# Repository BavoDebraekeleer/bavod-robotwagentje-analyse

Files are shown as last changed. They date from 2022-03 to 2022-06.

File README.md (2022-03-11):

# DocsifyJS Template 📒 🕸
> Starter template for a Markdown-based docs site







## Preview

<div align="center">
    <a href="https://michaelcurrin.github.io/docsify-js-template/">
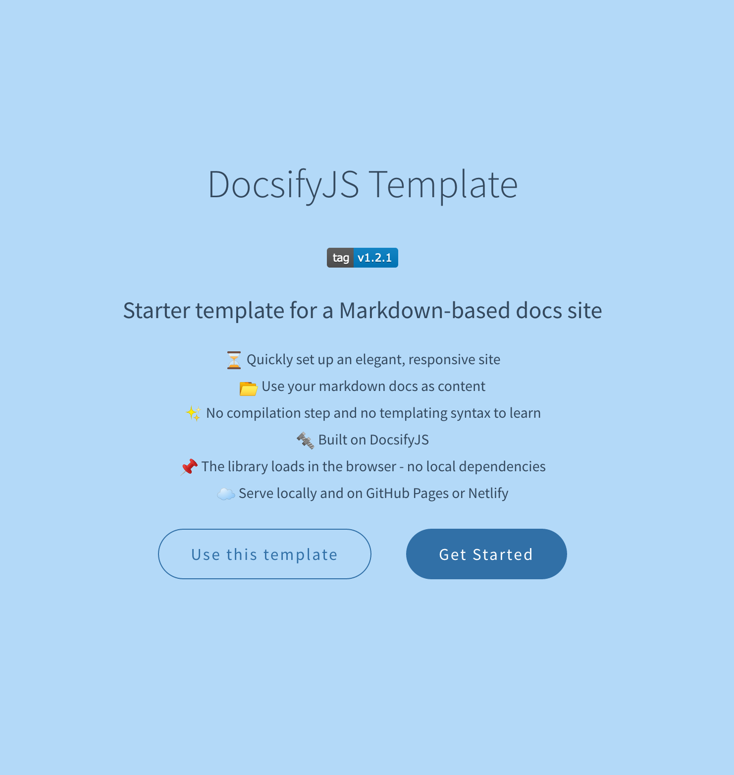
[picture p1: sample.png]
Sample screenshot
        
    </a>
</div>

<br>

<div align="center">



Instead of forking, rather make a new repo using this template button:



</div>

If you want to improve the original template, then fork it and make a PR.

## Features

- 🏭 Template for a SPA modern docs site.
- 📗 Use your awesome project's _existing_ markdown files.
- 🤩 Light on code – just add a single HTML file and optionally add cover page and navbar config.
- 🚀 Easy to host as a static site on GitHub Pages. No build step needed.

## Purpose
> How to use this project

- Create a **new repo** from the template and host it on GitHub Pages immediately. This is good for trying out Docsify or building a site project from scratch.
- Use this project as a **base** - follow instructions to download just the necessary files to your _existing_ repo's `docs` directory
- View the **live** demo site to see what you'll get.

For more info on Docsify, see my [DocsifyJS Tutorial][]. That covers intro to DocsifyJS, including installation, running and configuration. If you look at the repo, that has has more content and configuration than this relatively plain template site.

[DocsifyJS Tutorial]: https://michaelcurrin.github.io/docsify-js-tutorial/#/

## How to use Docsify in your projects

### Copy files

Use one of the approaches below to setup Docsify in your own project.

#### A. Use this template

Create a _new_ forked project based on this template  by clicking the button below. You'll get a fork in your own repo.



You could start adding code outside of the _docs_ directory, however this project is intended as a standalone docs site which can be configured for experimentation and used as reference.

#### B. Add Docsify to an existing project's docs directory

This will copy the contents of the docs directory from Github to the current folder - ideal if there is an existing project and you want to add to _Docsify_ it.

1. Ensure you have `curl` command installed. Or use `wget`.
2. Navigate to your project's `docs` folder.
    ```sh
    cd my-project/docs
    ```
3. Download necessary files in the template [docs](/docs) directory to your project using this two-line command. (The `-O` flag will save the files locally, keeping the original filenames.)
    ```sh
    REPO_DOCS='https://raw.githubusercontent.com/MichaelCurrin/docsify-js-template/master/docs/'
    curl $REPO_DOCS\{_coverpage.md,_sidebar.md,.nojekyll,index.html,README.md\} -O
    ```

### Customize

You can use your IDE to do find and replace across files.

Use the convenient [replace.sh](/replace.sh) script in this repo to replace the template's values with your own.

1. Find the script.
    - If you used the template button, you've already got it.
    - If adding content to your existing project's docs, copy script to your project **root** (not docs directory)
        ```sh
        curl 'https://raw.githubusercontent.com/MichaelCurrin/docsify-js-template/master/replace.sh' -O
        chmod +x ./replace.sh
        ```
2. Modify the `MY_` values then run this script to replace the template's value with your own.
3. Run the script from the **project root** against yours docs directory.
   ```sh
   ./replace.sh
   ```
4. The script can be deleted after you use it.

Now complete any remaining TODO items in the files.

### Use template readme

If you clicked _Use this template_, followed the customize steps above, then the last thing to do is replace the project's README.md file with the template one.

```sh
mv README.template.md README.md
```

Then customize README.md as your own project.

## Set up and run

### Remote use

Whatever approach you use to set up a `docs` directory, you can use your own project or a forked template and serve your site on platform like  GiHhub Pages or Netlify.

This template still works fine as a standalone online demo of _Docsify_ that you can tweak. In a real project, you'd add your code at the repo root, outside of `docs`. Or you could move your docs site to the repo root on the `gh-pages` branch for GH Pages.

### Serve locally

Follow this [gist](https://gist.github.com/MichaelCurrin/4c8060dcc9d8841f842eeebc7a1436d8) so you can view the docs site on a local webserver.

Go to my [DocsifyJS Tutorial - Serve locally](https://michaelcurrin.github.io/docsify-js-tutorial/#/?id=serve-a-docsify-site-locally) for more info on what DocsifyJS is and how to use it.

## Related projects

A template using Docsify Themeable. It is a Docsify site but easier to use, it is prettier (in my opinion), and supports a theme system that is more advanced than that in Docsify.

- 

A template for Vue-based docs site. Except it uses VuePress to render a static site (better for SEO) rather than as a Single-Page Application like Docsify.
 
- 

A template for a Vue-based app.

- 

## License

Released under [MIT](/LICENSE) by [@MichaelCurrin](https://github.com/MichaelCurrin).

- You can modify and reuse this project.
- Please link back to the original repo somewhere in your project if you use this in any way.
- Including an original license copy.
    - If you add content from [docs](/docs/) to your repo (or click _Use this template_) and then modify for your own needs so your copy is no longer a template, then you don't need to include a license.
    - If you do fork this repo then use it as your own _template_, then this project's license and copyright notice must be **included** with the software. [source](https://choosealicense.com/licenses/#mit). Copy `LICENSE` to `LICENSE-source` and then update your copy of `LICENSE` with your own details.

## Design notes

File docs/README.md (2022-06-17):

# Robotwagentje

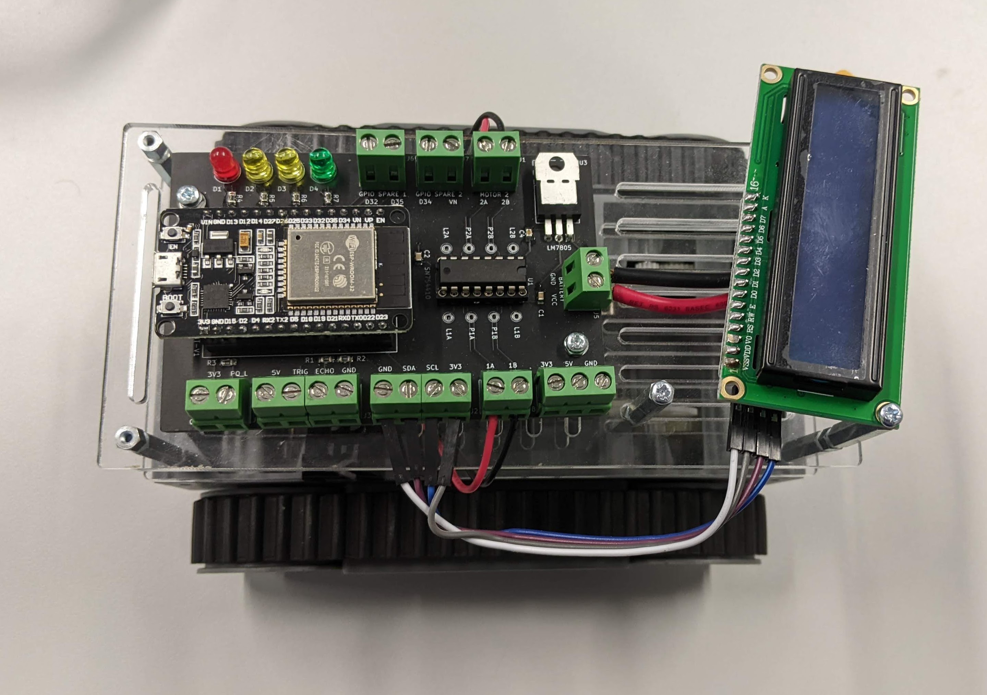
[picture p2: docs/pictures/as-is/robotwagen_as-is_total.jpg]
<br>

<br>

<br>
<br>
<br>
<br>
<br>
<br>

Bavo Debraekeleer<br>
Docent: Marc Smets en Maarten Luyts<br>

Smart Systems, major Internet of Things, Elektronica-ICT<br>
AP Hogeschool<br>
Academiejaar 2021-2022

<a href="https://bavodebraekeleer.github.io/bavod-robotwagentje-analyse/#/">Robotwagentje Analyse GitHub Pages</a><br>
<a href="https://ap-it-gh.github.io/ssys-cursus/#/deliverables/analyse">Smart Systems GitHub Pages</a><br>

---

# Probleemstelling

Ontwerp van een schakelingen om een robotwagentje aan te sturen.
Dit opgedeeld in twee deel schakelingen.
Een hoofd PCB met een ESP32, als ook een dochter PCB met een ATMega en sensoren om de sturing te kunnen realiseren.
De vereisten zijn omschreven in de To-Be Situatie.

---

## As-Is Situatie



Grote PCB met enkel through hole componenten en screw terminals.

Eigenschappen:
 - Gebruik ESP32-WROOM-32 Dev. Kit
 - Voltage Regulator LM7805 through hole
 - Motord river SN754410 through hole + 2x 2 motor pins: 1A, 1B, 2A, 2B
 - 4x LED's: 1x rood, 2x geel, 1x groen
 - LCD scherm module, I²C pins op PCB: GND, SDA, SCL, 3V3
 - Ultrasoon module aansluiting: 5V, TRIG, ECHO, GND
 - 3 voeding pins: 3V3, 5V, GND
 - 2 pin aansluiting: 3V3, PQ_L
 - 2x 2 GPIO spare pins

---

## To-Be Situatie of Systeemspecificaties

### Opdracht doelen

 - Sensoren toepassen in een praktische schakeling.
 - Voldoende materiaal genereren voor gebruik in het eerste jaar.
 - Besturing voorzien.

### Sturingsschakeling vereisten:

Dit is de hoofd PCB.

 - ESP32-WROVER-B microcontroller module zelf integreren in PCB.
 - SMD componenten gebruiken.
 - 2x UART connectoren
 - 3x I²C connectoren
 - Voltage regulator LDL1117 SMD
	- 5V
	- 3.3V
 - Polariteitsbeveiliging
 - 2x SMD Motor driver
	- 7.2V
	- 700mA (Start stroom = 6x nominale stroom)
	- Prijs < €1
	- EMK beveiligingsdiode in tegen polariteit. Misschien reeds aanwezig op IC. Best altijd extra diode bij plaatsen voor de zekerheid.
 - OLED-scherm met I²C-sturing op PCB
 - Mounting drill holes, voor bevestiging op wagentje
 - Batterij aansluiting (GND, VCC)

### Sensorenschakeling vereisten:

Samen op één dochter PCB of opgedeeld in meerdere PCB bordjes.

 - ATMega328p
 - Ultrasoon + IR afstandssensoren
 - 8 channel IR Line tracker

### Besturing

 - Modus selectie
 - Manuele bediengingsmodus
 - Automatisch rijden (afstandsmetingen)
 - Volgens vast patroon rijden (lijn volgen)

Er moeten ook een aantal verkeer signalisaties ontwikkeld worden zoals verkeerslichten, slagbomen, enz.<br>
Deze moeten dienen om de software van het wagentje te kunnen testen.

---

## Mindmap

### Interactieve Mindmap
<iframe width="1000" height="1000" src="https://miro.com/app/embed/uXjVOER2lsE=/?pres=1&frameId=3458764521281290834" frameBorder="0" scrolling="no" allowFullScreen></iframe>

### Mindmap afbeelding
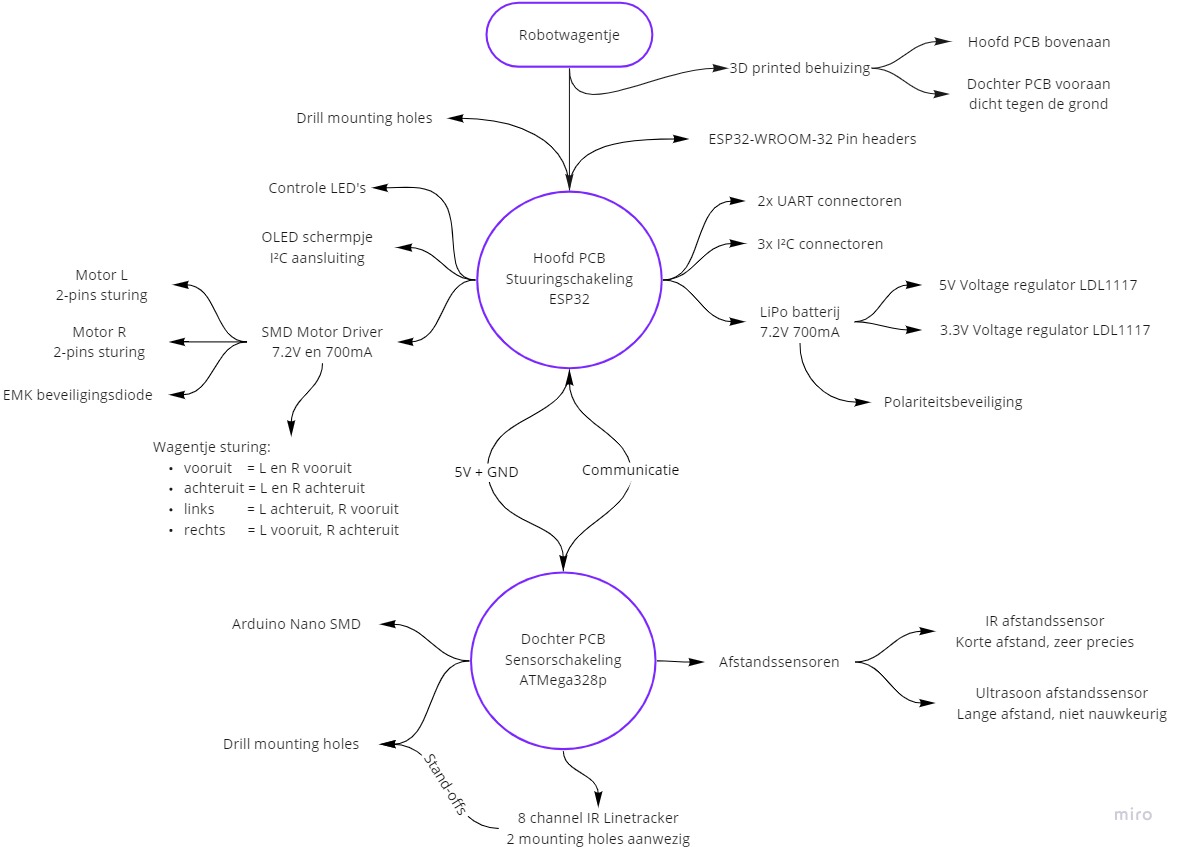
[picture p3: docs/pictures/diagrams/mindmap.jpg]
Mindmap afbeelding
<br>
<a href="./pictures/diagrams/mindmap.jpg">Minddmpa afbeelding openen.</a><br>

---

# Hardware Analyse

## Blokschema

### Interactief Blokschema
<iframe width="1000" height="1000" src="https://miro.com/app/embed/uXjVOEQMNko=/?pres=1&frameId=3458764523376607643" frameBorder="0" scrolling="no" allowFullScreen></iframe>

### Blokschema afbeelding
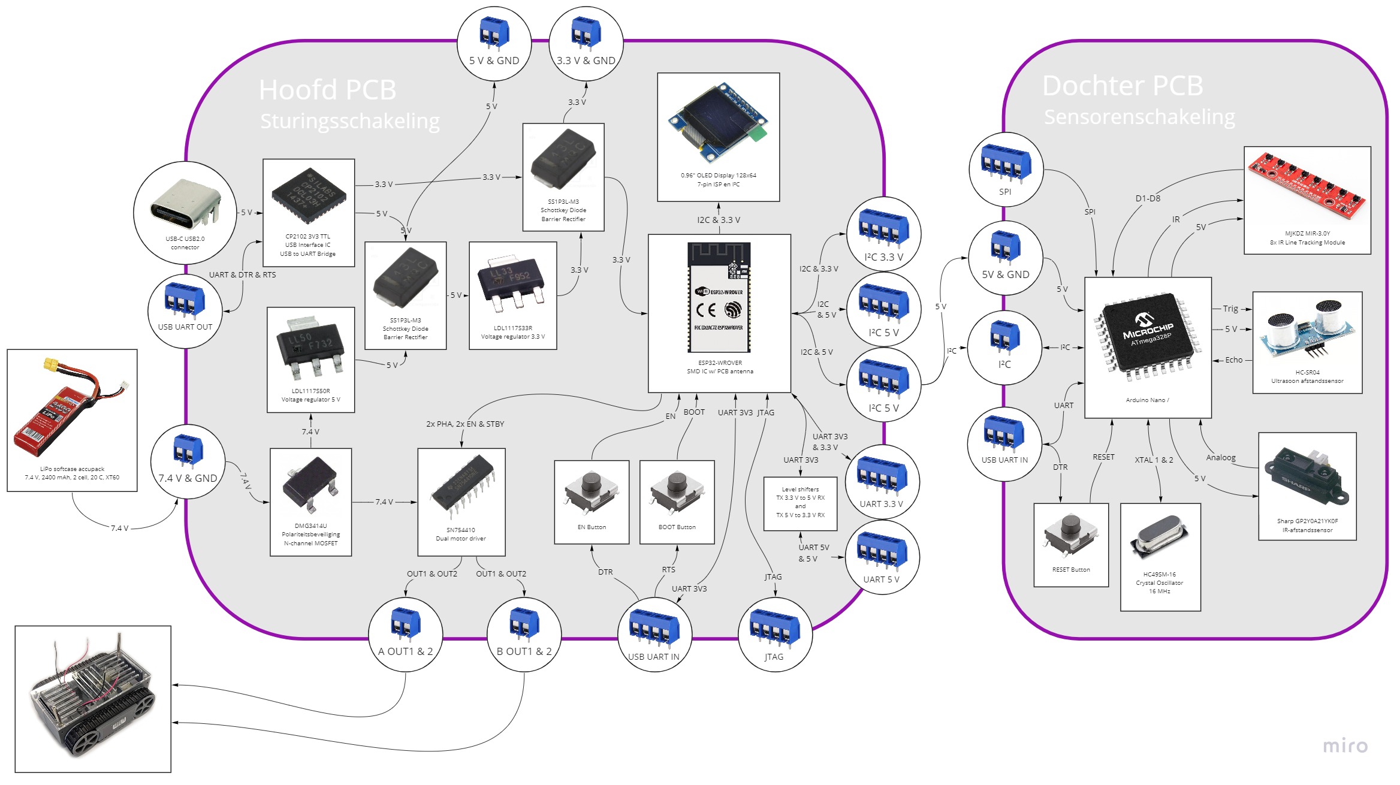
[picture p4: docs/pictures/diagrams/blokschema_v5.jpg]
Blokschema afbeelding
<br>
<a href="./pictures/diagrams/blokschema_v5.jpg">Blokschema afbeelding openen.</a><br>

---

## Specificaties

Reference websites:
 - <a href="https://be.farnell.com/">Farnell</a><br>
 - <a href="https://www.mouser.be/">Mouser</a><br>
 - <a href="https://www.digikey.be/">Digi-Key</a><br>
 - <a href="https://www.tinytronics.nl/shop/nl">TinyTronics</a><br>
 - <a href="https://octopart.com/">Octopart</a><br>
 - <a href="https://componentsearchengine.com/">Component Search Engine</a><br>

### Hoofd PCB: Sturingsschakeling

#### Microcontroller

<table style="width: 100%">
<colgroup>
    <col span="1" style="width: 15%;">
    <col span="2" style="width: 30%;">
    <col span="3" style="width: 40%;">
	<col span="4" style="width: 25%;">
</colgroup>
<tr>
    <th>Naam</th>
    <th>Eigenschappen</th>
    <th>Argumentatie</th>
    <th>Data</th>
</tr>
<tr>
    <td>ESP32-WROVER</td>
    <td>
        <ul>
            	<li><b>ESP32 REV1 microcontroller</b></li>
		<li>Core: ESP32-D0WDQ6</li>
		<li>SPI flash: 4 MB, 32 Mbits, 3.3 V</li>
		<li>PSRAM: 64Mbits</li>
		<li>Crystal: 40 MHz</li>
            	<li>V<sub>cc</sub> = 3.0 - 3.6 V</li>
            	<li>I<sub>operating</sub> = 80 mA</li>
		<li>I<sub>min delivered by power supply</sub> = 500 mA</li>
		<li>Module interfaces: SD card, UART, SPI, SDIO, I2C, LED PWM, Motor PWM, I2S, IR, pulse counter, GPIO, capacitive touch sensor, ADC, DAC, TWAI.</li>
		<li>On-chip sensor: Hall sensor</li>
		<li>Operating temperature: -40°C ~ +85°C</li>
		<li><i>Eenheidsprijs: €5,50</i></li>
		<li><i>Lead time: onbekend (op voorraad)</i></li>
        </ul>
    </td>
	<td>
		ESP32 module die beschikbaar is in het labo.
	</td>
    <td>
		<a href="./datasheets/esp32-wrover_datasheet_en-1223875.pdf">Datasheet Module</a><br>
		<a href="./datasheets/esp32_datasheet_en.pdf">Datasheet ESP32</a><br>
		<a href="./datasheets/esp32_hardware_design_guidelines_en.pdf">Hardware Design Guidelines</a><br>
		<a href="https://www.tinytronics.nl/shop/nl/communicatie-en-signalen/draadloos/wi-fi/modules/esp32-wrover-wifi-module-pcb-antenne-aansluiting">Winkel TinyTronics</a><br>
	</td>
</tr>
<tr>
    <td>ESP32-WROOM-32</td>
    <td>
        <ul>
            	<li><b>ESP32 microcontroller</b></li>
		<li>Core: ESP32-D0WD</li>
		<li>SPI flash: 4 MB, 32 Mbits, 3.3 V</li>
		<li>Crystal: 40 MHz</li>
            	<li>V<sub>cc</sub> = 3.0 - 3.6 V</li>
            	<li>I<sub>operating</sub> = 80 mA</li>
		<li>I<sub>min delivered by power supply</sub> = 500 mA</li>
		<li>Module interfaces: SD card, UART, SPI, SDIO, I2C, LED PWM, Motor PWM, I2S, IR, pulse counter, GPIO, capacitive touch sensor, ADC, DAC, TWAI.</li>
		<li>On-chip sensor: Hall sensor</li>
		<li>Operating temperature: -40°C ~ +85°C</li>
		<li><i>Eenheidsprijs: €4,68</i></li>
		<li><i>Lead time: 10 weken (op voorraad)</i></li>
        </ul>
    </td>
	<td>
		Alternatieve versie van de ESP32 module.
	</td>
    <td>
		<a href="./datasheets/esp32_wroom_32d_esp32_wroom_32u_datasheet_en-1365844.pdf">Datasheet Module</a><br>
		<a href="./datasheets/esp32_datasheet_en.pdf">Datasheet ESP32</a><br>
		<a href="./datasheets/esp32_hardware_design_guidelines_en.pdf">Hardware Design Guidelines</a><br>
		<a href="https://www.digikey.be/nl/products/detail/espressif-systems/ESP32-WROOM-32/8544298">Winkel Digi-Key</a><br>
		<a href="https://www.elektor.nl/wemos-lolin-esp32-oled-display-module-for-arduino"Alternatieve kit met OLED</a><br>
	</td>
</tr>
</table>

#### Sturing

<table style="width: 100%">
<colgroup>
    <col span="1" style="width: 15%;">
    <col span="2" style="width: 30%;">
    <col span="3" style="width: 40%;">
	<col span="4" style="width: 25%;">
</colgroup>
<tr>
    <th>Naam</th>
    <th>Eigenschappen</th>
    <th>Argumentatie</th>
    <th>Data</th>
</tr>
<tr>
    <td>SN754410NE</td>
    <td>
        <ul>
            	<li><b>Quadruple Half-H Driver</b></li>
		<li>Through-hole IC met 2 drivers</li>
		<li>Package: DIP</li>
            	<li>V<sub>cc</sub> = -0.5 - +36 V</li>
		<li>V<sub>O</sub> = -3 - +3 V</li>
            	<li>I<sub>O</sub> = ±1 A</li>
		<li>Power dissipation P<sub>D</sub> = 2.078 W</li>
		<li>Minimized Power Dissipation</li>
		<li><i>Eenheidsprijs: 2,93 - 2,48€</i></li>
		<li><i>Lead time: 26 weken (op voorraad)</i></li>
        </ul>
    </td>
    <td>
	    	Motor driver through-hole als vervanging door laattijdige beschikbaarheid van de TC78H621FN.
	    	Deze is duurder, maar was reeds beschikbaar in het labo.
	    	Heeft ook een veel betere power dissipatie.
	    	
	</td>
    <td>
		<a href="./datasheets/sn754410.pdf">Datasheet</a><br>
	    	<a href="https://www.ti.com/product/SN754410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">Website fabrikant</a><br>
		<a href="https://be.farnell.com/texas-instruments/sn754410ne/ic-peripheral-driver-half-h-1a/dp/3118977?ost=SN754410">Winkel Farnell</a><br>
	</td>
</tr>
<tr>
    <td>TC78H621FNG</td>
    <td>
        <ul>
            	<li><b>Stepping motor drivers</b></li>
		<li>Full, Half step resolution / Phase inputs</li>
		<li>2-phase bipolar stepper + full bridge driver</li>
		<li>SMD IC met 2 drivers</li>
		<li>Package: P-TSSOP16-0505-0.65-001</li>
            	<li>V<sub>cc</sub> = 2.8 - 14 V</li>
		<li>V<sub>OUT</sub> = 18 V</li>
            	<li>I<sub>OUT</sub> = 1.1 A</li>
		<li>Power dissipation P<sub>D</sub> = 0.78 W</li>
		<li><i>Eenheidsprijs: 1,66 - 0,82€</i></li>
		<li><i>Lead time: 26 weken (op voorraad)</i></li>
        </ul>
    </td>
    <td>
	    	Motor driver aangegeven door docent als te gebruiken IC en op voorraad in het labo.
	    	
	</td>
    <td>
		<a href="./datasheets/TC78H621FNG_TOSC-S-A0003869562-1.pdf">Datasheet</a><br>
	    	<a href="https://toshiba.semicon-storage.com/ap-en/semiconductor/product/motor-driver-ics/stepping-motor-driver-ics/detail.TC78H621FNG.html">Website fabrikant</a><br>
		<a href="https://www.digikey.com/en/products/detail/toshiba-semiconductor-and-storage/TC78H621FNG-EL/9351603">Winkel Digi-Key</a><br>
	</td>
</tr>
<tr>
    <td>LA6583MC-AH</td>
    <td>
        <ul>
            	<li><b>Motor driver</b></li>
		<li>Single Phase Driver With Hall Sensor Method (no Speed Control)</li>
		<li>SMD IC</li>
		<li>Output Configuration: Half Bridge, 2 outputs</li>
            	<li>V<sub>cc</sub> = 2.8 - 14 V</li>
		<li>V<sub>cc max</sub> = 15 V</li>
		<li>I<sub>cc drive</sub> = 4 - 6 - 9 mA</li>
            	<li>I<sub>OUT max</sub> = 800 mA</li>
		<li><i>Eenheidsprijs: 0,526€</i></li>
		<li><i>Lead time: onbekend (op voorraad)</i></li>
        </ul>
    </td>
    <td>
	    	Alternatieve Motor Driver als eerste voorgesteld door docent.
		Deze Motor Driver heeft twee outputs en wordt gebruikt om één motor aan te sturen in twee richtingen.
		Voor twee motors zijn er dus twee nodig in de schakeling.
		Een enkele IC om de twee motors aan te sturen komt veel duurder uit of zijn niet op voorraad.
		<a href="https://www.mouser.be/ProductDetail/Toshiba/TB6612FNGC8EL?qs=rsevcuukUAy2UalRuv4E%2FQ%3D%3D">Alternatief: TB6612FNG</a><br>
	</td>
    <td>
		<a href="./datasheets/LA6583MC-AH.pdf">Datasheet</a><br>
		<a href="https://be.farnell.com/on-semiconductor/la6583mc-ah/mtr-drvr-sngl-phase-fan-motor/dp/2728202?st=LA6583MC-AH">Winkel</a><br>
	</td>
</tr>
<tr>
    <td>Merkloos OLED 0.96" SPI</td>
    <td>
        <ul>
		<li><b>0.96" OLED Display 128x64</b></li>
		<li>V<sub>cc</sub> = 3.3 - 5 V</li>
		<li>I<sub>cc</sub> = 9 - 15 mA</li>
		<li>Controller: SSD1315</li>
		<li>Comm protocol: SPI of I²C</li>
		<li>Connector: 7 PIN's</li>
		<li>Afmetingen: 27.8 x 27.3 x 4.3 mm</li>
		<li>Drill holes: 2 mm diameter, ~1 mm van de rand</li>
		<li><i>Eenheidsprijs: €4,60 - €7,00</i></li>
		<li><i>Lead time: onbekend (op voorraad)</i></li>
        </ul>
    </td>
    <td>
		Er wordt hier gekozen voor een module omdat losse OLED displays moeilijk vindbaar zijn en/of duurder uitkomen, en meer werk zijn.
		Deze merkloze verzie is op voorraad in het labo en kan werken op I²C mits kleine aanpassingen aan de PCB.
		I²C aansluitingen: D0 = SCL, D1 = SDA, DC & CS = GND, RST = Solderen
		Goedkoper alternatief: Seeed Studio Grove 104020208
		<a href="https://www.distrelec.biz/en/ssd1315-grove-96-128-64-monochrome-oled-display-seeed-studio-104020208/p/30164993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">Winkel Distrelec</a><br>
		<a href="https://wiki.seeedstudio.com/Grove-OLED-Display-0.96-SSD1315/">Fabrikant product info</a><br>
		Enkele alternatieven van TinyTronics met I²C PIN connectors in meerdere formaten:
		<a href="https://www.tinytronics.nl/shop/nl/displays/oled/0.96-inch-oled-display-128*64-pixels-wit-i2c">0.96" 128x64 SSD1306 voor €7,00</a><br>
		<a href="https://www.tinytronics.nl/shop/nl/displays/oled/1.3-inch-oled-display-128*64-pixels-wit-i2c">1.3" 128x64 SSH1106 voor €8,00</a><br>
		<a href="https://www.tinytronics.nl/shop/nl/displays/oled/1.5-inch-oled-display-128*128-pixels-wit-i2c">1.5" 128x128 SSD1327 voor €10,00</a><br>
		 <a href="https://www.tinytronics.nl/shop/nl/kabels-en-connectoren/kabels-en-adapters/jst-compatible/wemos-i2c-kabel-sh1.0-4p-10cm">JST 4P kabel I²C</a><br>
		<a href="https://www.tinytronics.nl/shop/nl/kabels-en-connectoren/connectoren/jst-compatible/jst-xh-krimpstekker-en-behuizing-set">JST-HX stekkers set</a><br>
	</td>
    	<td>
		<a href="./datasheets/OEL_Display_Module_SJY-2864KSWPG01.pdf">OLED Module Datasheet</a><br>
		<a href="https://www.tinytronics.nl/shop/nl/displays/oled/0.96-inch-oled-display-128*64-pixels-blauw">Winkel TinyTronics</a><br>
		<a href="https://github.com/olikraus/u8g2">Bibliotheek: U8g2</a><br>
	</td>
</tr>
</table>

#### Voeding

<table style="width: 100%">
<colgroup>
    <col span="1" style="width: 15%;">
    <col span="2" style="width: 30%;">
    <col span="3" style="width: 40%;">
	<col span="4" style="width: 25%;">
</colgroup>
<tr>
    <th>Naam</th>
    <th>Eigenschappen</th>
    <th>Argumentatie</th>
    <th>Data</th>
</tr>
<tr>
    <td>Conrad Energy LiPo accupack</td>
    <td>
        <ul>
            	<li><b>LiPo softcase accupack</b></li>
            	<li>V<sub>nomonaal</sub> = 7.4 V</li>
            	<li>I<sub>nominaal</sub> =  1200 mAh</li>
		<li>Aantal cellen: 2</li>
		<li>Belastbaarheid: 20 C</li>
		<li>Aansluiting: XT60, XH-balancer</li>
		<li>Afmetingen: 112 x 35 x 19 mm</li>
		<li><i>Eenheidsprijs: €16,49</i></li>
		<li><i>Lead time: onbekend (op voorraad)</i></li>
        </ul>
    </td>
    <td>
		Zelfde batterij als in de As-Is situatie blijft behouden.
	</td>
    <td>
		<a href="./datasheets/accu.pdf">Datasheet</a>
		<a href="https://www.conrad.be/nl/p/conrad-energy-lipo-accupack-7-4-v-2400-mah-aantal-cellen-2-20-c-softcase-xt60-1344133.html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">Winkel Conrad</a><br>
	</td>
</tr>
<tr>
    <td>LDL1117S50R</td>
    <td>
        <ul>
            	<li><b>Voltage Regulator 5 V</b></li>
		<li>Package: SOT223 SMD</li>
		<li>V<sub>output</sub> = 5 V</li>
            	<li>V<sub>input</sub> = 2.5 - 18 V</li>
            	<li>I<sub>output</sub> = 1.2 A</li>
		<li><i>Eenheidsprijs: €0,56</i></li>
		<li><i>Lead time: 52 weken (lage voorraad)</i></li>
        </ul>
    </td>
    <td>
		Eenvoudige en goedkope LDO regulator.
		Alternatieven die 3.3 en 5 V in één package doen hebben een lage I<sub>output</sub>.
		Alternatief voorbeeld:
		<a href="https://www.mouser.be/ProductDetail/Microchip-Technology-Micrel/MIC5211-LXYM6-TR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">MIC5211-LXYM6-TR</a>
    </td>
    <td>
		<a href="./datasheets/LDL1117_algemeen.pdf">Datasheet algemeen</a><br>
		<a href="./datasheets/LDL1117_SOT223_specific.pdf">Datasheet SOT223</a><br>
		<a href="https://www.mouser.be/ProductDetail/STMicroelectronics/LDL1117S50R?qs=AQlKX63v8RsuN9BQFiVf%2Fg%3D%3D">Winkel Mouser</a><br>
		<a href="https://www.avnet.com/shop/us/products/stmicroelectronics/ldl1117s50r-3074457345642528941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">Winkel AVNET (op voorraad)</a>
	</td>
</tr>
</table>
<table style="width: 100%">
<colgroup>
    <col span="1" style="width: 15%;">
    <col span="2" style="width: 30%;">
    <col span="3" style="width: 40%;">
	<col span="4" style="width: 25%;">
</colgroup>
<tr>
    <td>LDL1117S33R</td>
    <td>
        <ul>
            	<li><b>Voltage Regulator</b></li>
		<li>Package: SOT-223 SMD</li>
		<li>V<sub>output</sub> = 5 V</li>
            	<li>V<sub>input</sub> = 2.5 - 18 V</li>
            	<li>I<sub>output</sub> = 1.2 A</li>
		<li><i>Eenheidsprijs: €0,56</i></li>
		<li><i>Lead time: 52 weken (op voorraad)</i></li>
        </ul>
    </td>
    <td>
		Eenvoudige en goedkope LDO regulator.
		Alternatieven die 3.3 en 5 V in één package doen hebben een lage I<sub>output</sub>.
	</td>
    <td>
		<a href="./datasheets/LDL1117_algemeen.pdf">Datasheet algemeen</a><br>
		<a href="./datasheets/LDL1117_SOT223_specific.pdf">Datasheet SOT223</a><br>
		<a href="https://www.mouser.be/ProductDetail/STMicroelectronics/LDL1117S33R?qs=AQlKX63v8Rt9Bf6AWSrbFg%3D%3D">Winkel Mouser</a><br>
		<a href="https://uk.farnell.com/stmicroelectronics/ldl1117s33r/ldo-fixed-3-3v-1-2a-sot-223-3/dp/2729708?st=ldl1117s33r">Winkel Farnell</a><br>
	</td>
</tr>
<tr>
    <td>DMG3414U</td>
    <td>
        <ul>
            	<li><b>Polariteitsbeveiliging N-channel MOSFET</b></li>
		<li>Package: SOT-23 SMD</li>
            	<li>V<sub>ds</sub> = 20 V</li>
            	<li>I<sub>d</sub> = 4.2 A</li>
		<li>R<sub>ds(on)</sub> = 0.019 ohm</li>
		<li>V<sub>gs(th)</sub> = 500 mV</li>
		<li>P<sub>d</sub> = 780 mW</li>
		<li><i>Eenheidsprijs: 0,72€</i></li>
		<li><i>Lead time: 52 weken (op voorraad)</i></li>
        </ul>
    </td>
    <td>
		Een N-channel MOSFET met lage R<sub>ds(on)</sub> op de negatieve voedingslijn geeft de beste batterij levensduur volgens onderzoek.
		De DMG3414U heeft een lage threshold spanning zodat deze ook geleid bij lage spanningen, en een V<sub>ds</sub> en I<sub>d</sub> die hoog genoeg zijn zodat de MOSFET niet stuk gaat in deze schakeling met 7.2 V batterij.
		<a href="./datasheets/Polariteitsbeveiliging_dt94-8.pdf">Polariteitsbeveiliging onderzoek</a><br>
		<a href="http://www.irf.com/technical-info/designtp/dt94-8.pdf">Web download (bron)</a><br>
		<a href="https://www.elektormagazine.nl/magazine/elektor-199907/39665>Uitleg.</a><br>
		<a href="https://www.circuitsonline.net/forum/view/50988>Uitleg.</a><br>
	</td>
    <td>
		<a href="./datasheets/DMG3414U_N-MOSFET.pdf">Datasheet</a><br>
		<a href="https://nl.farnell.com/diodes-inc/dmg3414u/mosfet-n-ch-w-diode-20v-4-2a-sot23/dp/2061404?st=mosfet%20n%20smd">Winkel Farnell</a><br>
	</td>
</tr>
<tr>
    <td>Mini USB type B connector</td>
    <td>
        <ul>
            	<li><b>SMD USB connector</b></li>
		<li>Package: SMD/SMT</li>
		<li>V<sub>nom</sub> = 30 V</li>
		<li>I<sub>nom</sub> = 1 A</li>
            	<li>Number of contacts: 5</li>
            	<li>Isolatieweerstand: 100 MOhms</li>
		<li><i>Eenheidsprijs: ~€1,00</i></li>
		<li><i>Lead time: 32 weken (op voorraad)</i></li>
        </ul>
    </td>
    <td>
	    	Alternatieve USB-poort.
		Om het testen en programmeren eenvoudiger te maken wordt er gekozen om ook een Mini USB poort te voorzien.
		Deze kan 5V voeding voorzien en als aangesloten op een UART poort ook de microcontrollers programmeren zoals het is op de Arduino Nano.
		Hiervoor is er ook het volgende component nodig, een USB Interface IC met USB naar UART Bridge.
    </td>
    <td>
		<a href="./datasheets/molex_USB-Mini-B_SMDconnector.pdf">Datasheet</a><br>
		<a href="https://eu.mouser.com/ProductDetail/Molex/67503-1020?qs=7zcQ9RRVJlhHWuXYKEhKMg%3D%3D">Winkel Mouser</a><br>
	</td>
</tr>
<tr>
    <td>USB4085-GF-A</td>
    <td>
        <ul>
            	<li><b>USB-C USB2.0 connector</b></li>
		<li>Package: through hole</li>
		<li>V<sub>rating</sub> = 20 V DC</li>
		<li>I<sub>rating VBUS</sub> = 3.00 A</li>
		<li>I<sub>rating GND</sub> = 4.25 A</li>
		<li>I<sub>rating VCONN</sub> = 1.25 A</li>
		<li>I<sub>rating other pins</sub> = 0.25 A</li>
		<li><i>Eenheidsprijs: €0,92 - 0,64</i></li>
		<li><i>Lead time: 16 weken (op voorraad)</i></li>
        </ul>
    </td>
    <td>
	    	Alternatieve USB-poort op voorraad in het labo, maar wel through-hole.
	    	Voordeel van future proofing met USB-C tegenover andere USB types.
    </td>
    <td>
		<a href="./datasheets/USB-C_2.0_USB4085-GF-A.pdf">Datasheet</a><br>
		<a href="https://www.digikey.nl/nl/products/detail/gct/USB4085-GF-A/9859733">Winkel Digi-Key</a><br>
	</td>
</tr>
<tr>
    <td>USB4110-GF-A</td>
    <td>
        <ul>
            	<li><b>USB-C USB2.0 SMD connector</b></li>
		<li>Klemtype: through hole</li>
		<li>V<sub>rating</sub> = 20 V DC</li>
		<li>I<sub>rating VBUS</sub> = 3.00 A</li>
		<li>I<sub>rating GND</sub> = 4.25 A</li>
		<li>I<sub>rating VCONN</sub> = 1.25 A</li>
		<li>I<sub>rating other pins</sub> = 0.25 A</li>
		<li><i>Eenheidsprijs: €1,27 - 0,79</i></li>
		<li><i>Lead time: 16 weken (op voorraad)</i></li>
        </ul>
    </td>
    <td>
	    	Gebruikte USB-poort. SMD versie van de USB4085-GF-A en gemakkelijker met de hand soldeerbaar, maar iets duurder.
	    	Voordeel van future proofing met USB-C.
    </td>
    <td>
		<a href="./datasheets/USB4110-2888203.pdf">Datasheet</a><br>
		<a href="https://www.mouser.be/ProductDetail/640-USB4110-GF-A">Winkel Mouser</a><br>
	</td>
</tr>
<tr>
    <td>FTDI FT232RL-REEL</td>
    <td>
        <ul>
            	<li><b>USB Interface IC: USB naar UART Bridge</b></li>
		<li>Package: SSOP-28 SMD/SMT</li>
		<li>V<sub>cc</sub> = 3.3 - 5.25 V</li>
		<li>I<sub>operationeel</sub> = 25 mA</li>
            	<li>Standaard: USB 2.0</li>
            	<li>Interfacetype: UART</li>
		<li><i>Eenheidsprijs: ~€3,00 - 4,00</i></li>
		<li><i>Lead time: onbekend (niet op voorraad)</i></li>
        </ul>
    </td>
    <td>
	    	Alternatief.
		Dit component is nodig om de USB poort te verbinden met de microcontroller.
		Verder zijn volgende componenten, naast weerstanden en condensatoren, vereist voor een correcte werking:
		<ul>
            		<li>Schottky Diode: <a href="https://octopart.com/ss1p3l-m3%2F84a-vishay-42865893?r=sp">SS1P3L</a> of <a href="https://octopart.com/mbr0520lt1g-onsemi-2933?r=sp">MBR0520LT1</a></li>
			<li>Fuse/zekering: <a href="https://octopart.com/mf-fsmf050x-2-bourns-10470804?r=sp">MFFSMF050</a></li>
			<li>Reset knop: <a href="https://eu.mouser.com/ProductDetail/CK/PTS636-SK50-SMTR-LFS?qs=vLWxofP3U2y5oRNZdHfrFw%3D%3D">PTS363</a> of <a href="https://eu.mouser.com/ProductDetail/Panasonic/EVQ-P2F02K?qs=WwqriLBepZsV0QucKJ89rg%3D%3D">EVQ-P2F02K</a>
        	</ul>
    </td>
    <td>
		<a href="./datasheets/DS_FT232R_USB-UART.pdf">Datasheet</a><br>
		<a href="https://eu.mouser.com/ProductDetail/Molex/67503-1020?qs=7zcQ9RRVJlhHWuXYKEhKMg%3D%3D">Winkel Mouser</a><br>
		<a href="https://uk.farnell.com/ftdi/ft232rl-reel/ic-usb-to-uart-smd-28ssop/dp/1146032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">Winkel Farnell</a><br>
		<a href="https://www.digikey.be/en/products/detail/FT232RL-REEL/768-1007-6-ND/1836408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">Winkel Digi-Key</a><br>
	</td>
</tr>
<tr>
    <td>CP2102N-A02-GQFN28R</td>
    <td>
        <ul>
            	<li><b>USB Interface IC: USB naar UART Bridge</b></li>
		<li>Package: QFN-28 SMD/SMT</li>
		<li>V<sub>cc</sub> = 3.0 - 3.6 V</li>
		<li>I<sub>operationeel</sub> = 13.7 mA</li>
            	<li>Standaard: USB 2.0</li>
            	<li>Interfacetype: UART</li>
		<li><i>Eenheidsprijs: ~€2,00</i></li>
		<li><i>Lead time: 40 weken (niet op voorraad)</i></li>
        </ul>
    </td>
    <td>
		Gebruikte USB interface die op voorraad is in het labo en daarom gebruikt wordt.
    </td>
    <td>
		<a href="./datasheets/CP2102N-A02-GQFN28R.pdf">Datasheet</a><br>
		<a href="https://eu.mouser.com/ProductDetail/Silicon-Labs/CP2102N-A02-GQFN28R?qs=u16ybLDytRag4qKvSH3fTw%3D%3D">Winkel Mouser</a><br>
		<a href="https://www.digikey.com/en/products/detail/CP2102N-A02-GQFN28R/336-5890-1-ND/9863483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">Winkel Digi-Key</a><br>
	</td>
</tr>
<tr>
    <td>TXU0204QPWRQ1 Level Shifter</td>
    <td>
        <ul>
            	<li><b>4 bit Fixed Direction Voltage Level Translator</b></li>
		<li>Package: TSSOP-14 SMD/SMT</li>
		<li>V<sub>cc</sub> = 1.08 - 5.5 V</li>
		<li>I<sub>operationeel</sub> = 6 uA</li>
		<li>Signaalvertraging 96 ns</li>
            	<li>Aantal kanalen: 4 channel</li>
            	<li>Push-pull level shifting: UART, SPI, JTAG</li>
		<li>Uitgangstype: 3-State</li>
		<li>Datasnelheid: 200 Mb/s
		<li><i>Eenheidsprijs: ~€0,42 - 0,94</i></li>
		<li><i>Lead time: 9 weken (op voorraad)</i></li>
        </ul>
    </td>
    <td>
	    	Alternatief. Zelf met componenten level shifter gemaakt.
		Om de USB interface ook te kunnen gebruiken voor de ESP32, die logische niveaus heeft van 3.3 V ipv 5 V, is er een level shifter nodig.
		De UART verbinding kan ook gebruikt worden om met andere toestellen te communiceren met logische niveaus van 5 V.
	    	Uiteindelijk niet gebruikt. Door alternatieve USB interface die op 3.3 V TTL werkt is er maar één opttionele level shifter meer nodig en deze wordt opgebouwd zonder IC.
    </td>
    <td>
		<a href="./datasheets/Level_Shifter_TXU0204QPWRQ1.pdf">Datasheet</a><br>
		<a href="https://eu.mouser.com/ProductDetail/Texas-Instruments/TXU0204QPWRQ1?qs=QNEnbhJQKvbo%252BW7%2Fo1U3Qg%3D%3D">Winkel Mouser</a>
	</td>
</tr>
</table>

---

### Dochter PCB: Sensorenschakeling

#### Microcontroller

<table style="width: 100%">
<colgroup>
    <col span="1" style="width: 15%;">
    <col span="2" style="width: 30%;">
    <col span="3" style="width: 40%;">
	<col span="4" style="width: 25%;">
</colgroup>
<tr>
    <th>Naam</th>
    <th>Eigenschappen</th>
    <th>Argumentatie</th>
    <th>Data</th>
</tr>
<tr>
    <td>ATMega328p-AN</td>
    <td>
        <ul>
            <li>SPI flash: 4 MB, 32 Mbits, 3.3 V</li>
            <li>V<sub>cc</sub> = 5 V</li>
            <li>V<sub>max</sub> = 6 - 20 V</li>
	    <li>I<sub>per I/O pin</sub> = 40 mA</li>
	    <li>I<sub>3V3 I/O pin</sub> = 50 mA</li>
	    <li><i>Eenheidsprijs: ~ €3,00</i></li>
	    <li><i>Lead time: 76 weken (niet op voorraad)</i></li>
        </ul>
    </td>
    <td>
		De sensoren moeten op een apart bordje komen zodat de line tracker dicht tegen de grond zit.
		Omdat hiervoor zeer veel verbindingen vereist zijn is het eenvoudiger om een extra microcontroller te voorzien.
		Op die manier is er maar één enkele I²C verbinding nodig tussen de twee bordjes.
		Er wordt hier gekozen om een ATMega328p te embedden in de PCB zodat een vergelijkbare schakeling aan de Arduino Nano wordt bekomen.
		Iets waarmee studenten reeds vertrouwd zijn en een goede oefening.
    </td>
    <td>
		<a href="./datasheets/ATMega328p.pdf">Datasheet ATMega328p</a><br>
		<a href="./datasheets/Arduino_Nano.pdf">Datasheet Arduino Nano</a><br>
		<a href="https://docs.arduino.cc/hardware/nano">Officiële documentatie Arduino Nano</a><br>
		<a href="https://store.arduino.cc/products/arduino-nano">Winkel Arduino</a><br>
		<a href="https://octopart.com/search?q=ATMega328p-a&currency=USD&specs=0">Winkels</a><br>
	</td>
</tr>
<tr>
    <td>Crystal HC49SM-16-30-50-60-16-ATF</td>
    <td>
        <ul>
	    <li>Frequency nominal: 16 MHz</li>
            <li>Frequency stability: 50 ppm</li>
            <li>Load capacitance: 16 pF</li>
	    <li>Crystal case: SMD, 11.4 x 4.65 mm</li>
	    <li><i>Eenheidsprijs: €0,284</i></li>
	    <li><i>Lead time: onbekend (op voorraad)</i></li>
        </ul>
    </td>
    <td>SMD crystal voor de ATMega.</td>
    <td>
		<a href="./datasheets/Crystal_HC49SM_1667017.pdf">Datasheet</a><br>
		<a href="https://be.farnell.com/multicomp/hc49sm-16-30-50-60-16-atf/crystal-hc-49-4hsmx-16-0mhz/dp/1667017RL">Winkel Farnell</a>
    </td>
</tr>
<tr>
    <td>PCF8574</td>
    <td>
	<ul>
		<li><b>Remote 8-bit I/O Expander I²C</b></li>
		<li>V<sub>cc</sub> = 2.5 - 6 V</li>
		<li>I<sub>cc Operating</sub> = 40 - 100 μA</li>
		<li>I<sub>cc Standby</sub> = 2.5 - 10 μA</li>
		<li><i>Eenheidsprijs: €</i></li>
		<li><i>Lead time: </i></li>
        </ul>
    </td>
    <td>
		Als alternatief voor het werken met een extra microcontroller kan er ook gebruik gemaakt worden voor een I/O expander.
		Deze kan de D1-D8 outputs van de line tracker's IR sensors opvangen en via I²C doorsturen waardoor de de vereiste GPIO pins op de ESP32 herleid worden naar 3.
	</td>
    <td>
		<a href="./datasheet/PCF8574_IOExpander_TI.pdf">Datasheet TI</a><br>
		<a href="./datasheet/PCF8574_IOExpander_NXP.pdf">Datasheet NXP</a><br>
		<a href="https://www.mouser.be/ProductDetail/Texas-Instruments/PCF8574DGVR?qs=wgAEGBTxy7kn%2FU04Mebwcg%3D%3D">Winkel Mouser PCF8574DGVR</a><br>
		<a href="https://be.farnell.com/nxp/pcf8574t-3-512/i-o-expander-8bit-remote-so-16/dp/1506644?st=pcf8574">Winkel Farnell PCF8574T/3,512</a><br>
	</td>
</tr>
</table>

#### Sensoren

<table style="width: 100%">
<colgroup>
    <col span="1" style="width: 15%;">
    <col span="2" style="width: 30%;">
    <col span="3" style="width: 40%;">
	<col span="4" style="width: 25%;">
</colgroup>
<tr>
    <th>Naam</th>
    <th>Eigenschappen</th>
    <th>Argumentatie</th>
    <th>Data</th>
</tr>
<tr>
    <td>MJKDZ MIR-3.0Y</td>
    <td>
        <ul>
            	<li><b>8x IR Line Tracking Module</b></li>
            	<li>V<sub>cc</sub> = 3 - 5 V</li>
            	<li>I<sub>max</sub> = ? mA</li>
		<li>Bereik (max. bij 5V) = 40 mm</li>
		<li>Afmetingen LxB: 17 x 67 mm</li>
		<li><i>Eenheidsprijs: €6,00</i></li>
		<li><i>Lead time: onbekend (op voorraad)</i></li>
        </ul>
    </td>
    <td>
		Gegeven in de opgave.
		
		Alternatief met PIN uitleg: <a href="https://einstronic.com/product/hy-s301-8-channel-line-tracking-sensor-module/">HY-S301</a><br>
	</td>
    <td>
		<a href="http://www.mjkdz.com/mjkdz/products/18365968.html">Fabrikant website</a><br>
		<a href="https://www.tinytronics.nl/shop/nl/sensoren/optisch/infrarood/8x-ir-lijn-tracking-module-40mm-bereik">Winkel TinyTronics</a><br>
	</td>
</tr>

<tr>
    <td>Sharp GP2Y0A21YK0F</td>
    <td>
        <ul>
		<li><b>IR-afstandssensor</b></li>
		<li>V<sub>cc</sub> = 4.5 - 5.5 V</li>
		<li>I<sub>typ</sub> = 30 mA</li>
		<li>Bereik: 50 - 800 mm</li>
		<li>Afmetingen: 29.5 x 13 x 13.5 mm</li>
		<li><i>Eenheidsprijs: €5,50 - 12,06</i></li>
		<li><i>Lead time: 16 weken (op voorraad)</i></li>
        </ul>
    </td>
    <td>
		Op voorraad in het labo.
		Mogelijke variaties in exacte type en de bijhorende output spanning.
	</td>
    <td>
		<a href="./datasheets/Sharp_GP2Y0A21YK0F.pdf">Datasheet</a><br>
		<a href="https://www.tinytronics.nl/shop/nl/sensoren/afstand/sharp-optische-afstandsensor-gp2y0a21yk0f">Winkel TinyTronics</a><br>
		<a href="https://be.farnell.com/sharp/gp2y0a21yk0f/sensor-distance-analogue/dp/1243869?ost=gp2y0a21yk0f">Winkel Farnell</a><br>
		<a href="https://www.mouser.be/ProductDetail/Sharp-Microelectronics/GP2Y0A21YK0F?qs=5S%2F4hkdqNNcI0gpWLEuQ8w%3D%3D">Winkel Mouser</a><br>
	</td>
</tr>
<tr>
    <td>HC-SR04</td>
    <td>
        <ul>
           	<li><b>Ultrasoon afstandssensor</b></li>
           	<li>V<sub>cc</sub> = 5 V</li>
           	<li>I<sub>cc</sub> = <2 - 15 mA</li>
			<li>Bereik: 20 - 4500 mm</li>
			<li>Resolutie: 3 mm</li>
			<li>Sensor hoek: <15°</li>
			<li>Ultrasone freq.: 40 kHz</li>
			<li><i>Eenheidsprijs: €3,00 - 7,21</i></li>
			<li><i>Lead time: 16 weken (op voorraad)</i></li>
        </ul>
    </td>
    <td>
		Op voorraad in het labo.
		Wat variatie in technische gegevens tussen leveranciers. Goed nakijken of het 3 V of 5 V logica betreft.
	</td>
    <td>
		<a href="./datasheets/distance_measurement_ultrasound_hcsr04-2489278.pdf">Datasheet</a><br>
		<a href="./datasheets/HC-SR04_Adafruit_Product_Overview_3942.pdf">Data and application notes.</a><br>
		<a href="https://www.tinytronics.nl/shop/nl/sensoren/afstand/ultrasonische-sensor-hc-sr04">Winkel TinyTronics</a><br>
		<a href="https://www.mouser.be/ProductDetail/Adafruit/3942?qs=byeeYqUIh0OD1hDPcrj%252BAQ%3D%3D">Winkel Mouser (Adafruit)</a><br>
		<a href="https://www.mouser.be/ProductDetail/OSEPP-Electronics/HC-SR04?qs=wNBL%252BABd93PqZEhuhHkuOw%3D%3D">Winkel Mouser (SEPP)</a><br>
		<a href="https://www.osepp.com/downloads/HCSR04_Library.zip">OSEPP Library</a><br>
		<a href="https://create.arduino.cc/projecthub/abdularbi17/ultrasonic-sensor-hc-sr04-with-arduino-tutorial-327ff6">Arduino tutorial</a><br>
	</td>
</tr>
</table>

---

## Elektrische Schema's en PCB's

### Sturingsschakeling

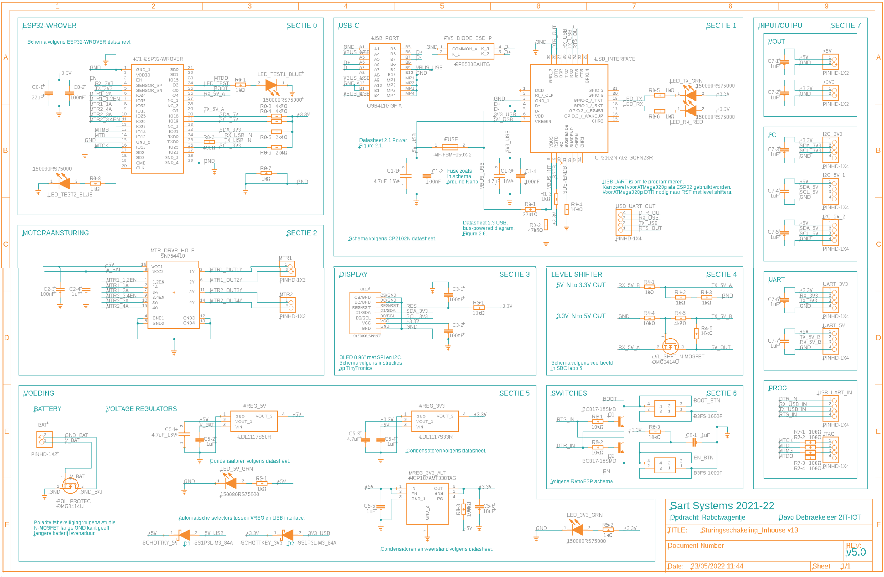
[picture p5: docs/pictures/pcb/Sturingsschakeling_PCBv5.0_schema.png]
<br>
<a href="./pictures/pcb/Sturingsschakeling_schema_v5.0.fsch">Schematic File</a><br>

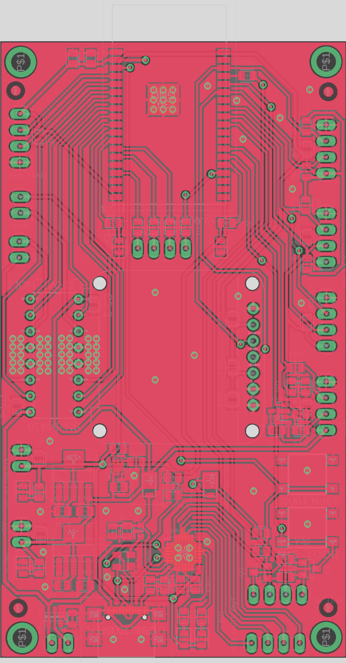
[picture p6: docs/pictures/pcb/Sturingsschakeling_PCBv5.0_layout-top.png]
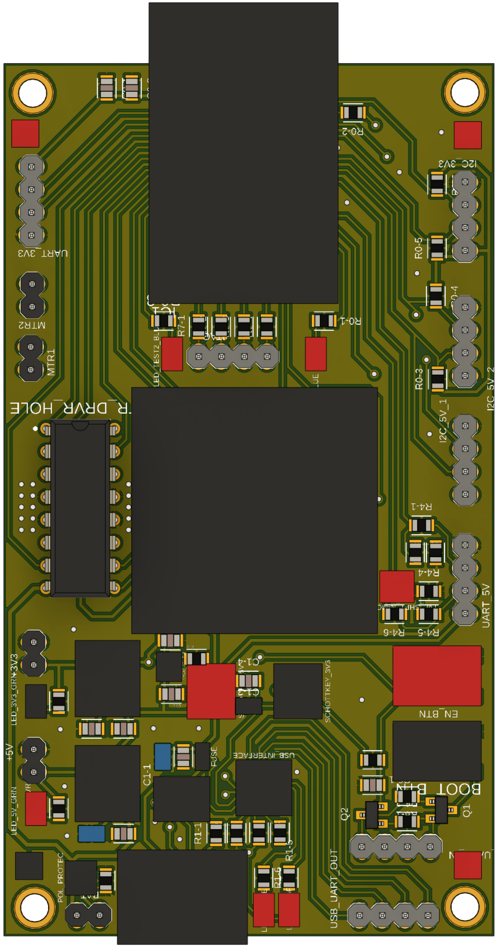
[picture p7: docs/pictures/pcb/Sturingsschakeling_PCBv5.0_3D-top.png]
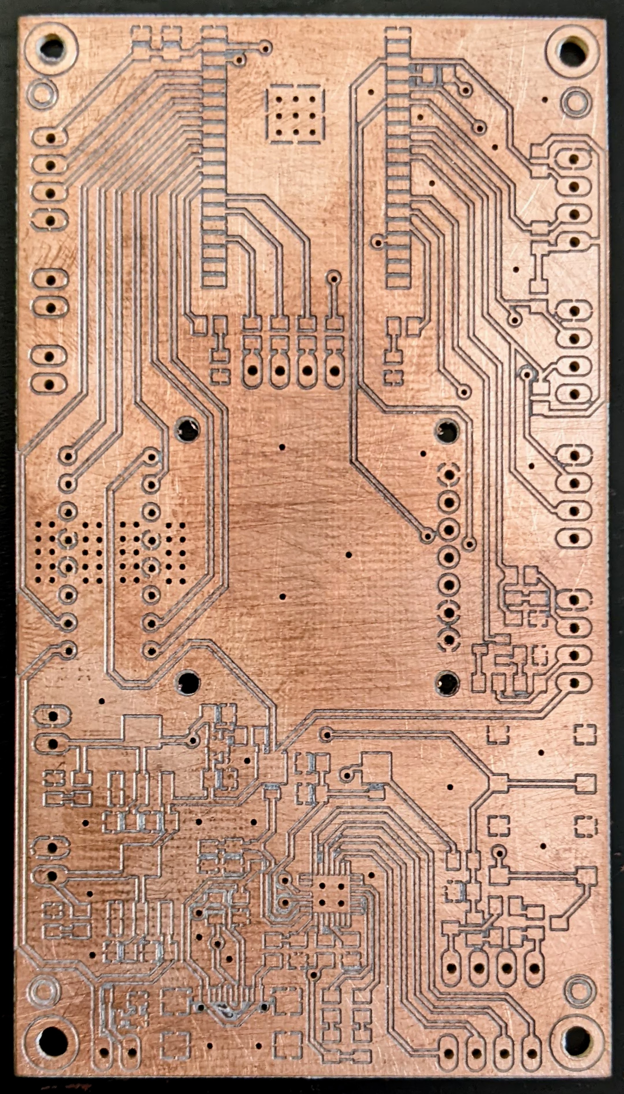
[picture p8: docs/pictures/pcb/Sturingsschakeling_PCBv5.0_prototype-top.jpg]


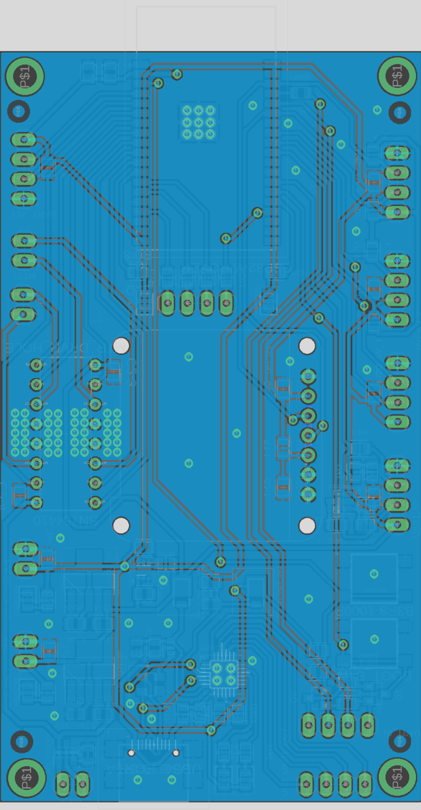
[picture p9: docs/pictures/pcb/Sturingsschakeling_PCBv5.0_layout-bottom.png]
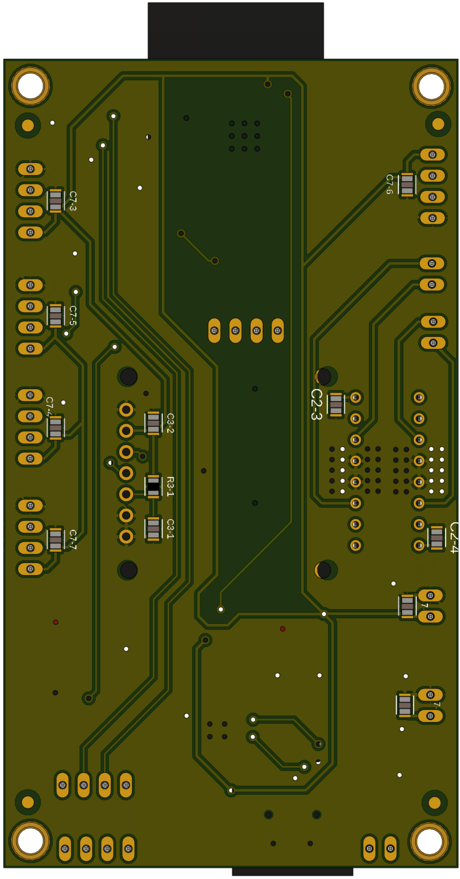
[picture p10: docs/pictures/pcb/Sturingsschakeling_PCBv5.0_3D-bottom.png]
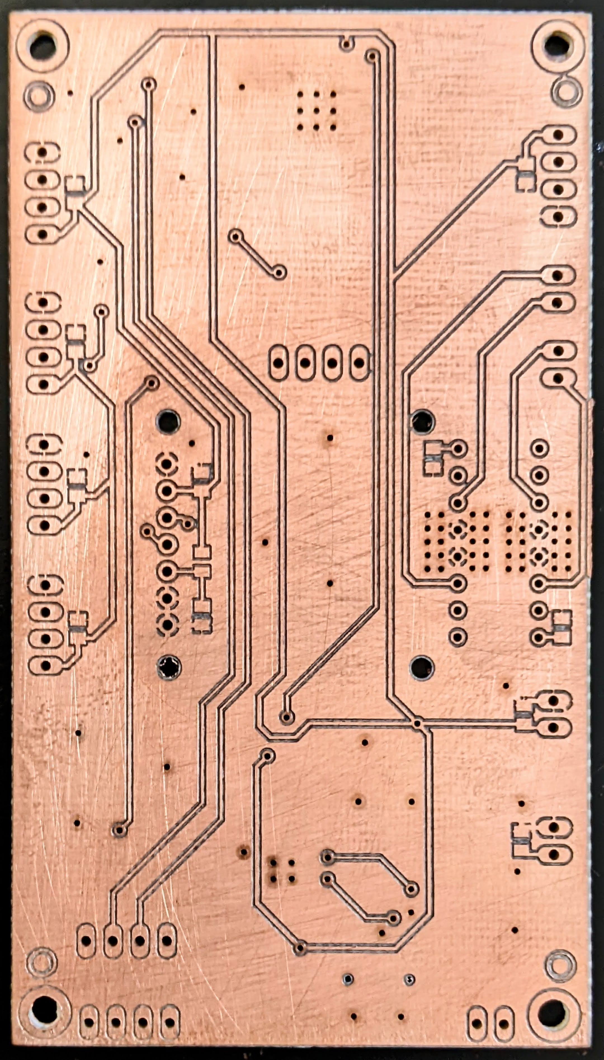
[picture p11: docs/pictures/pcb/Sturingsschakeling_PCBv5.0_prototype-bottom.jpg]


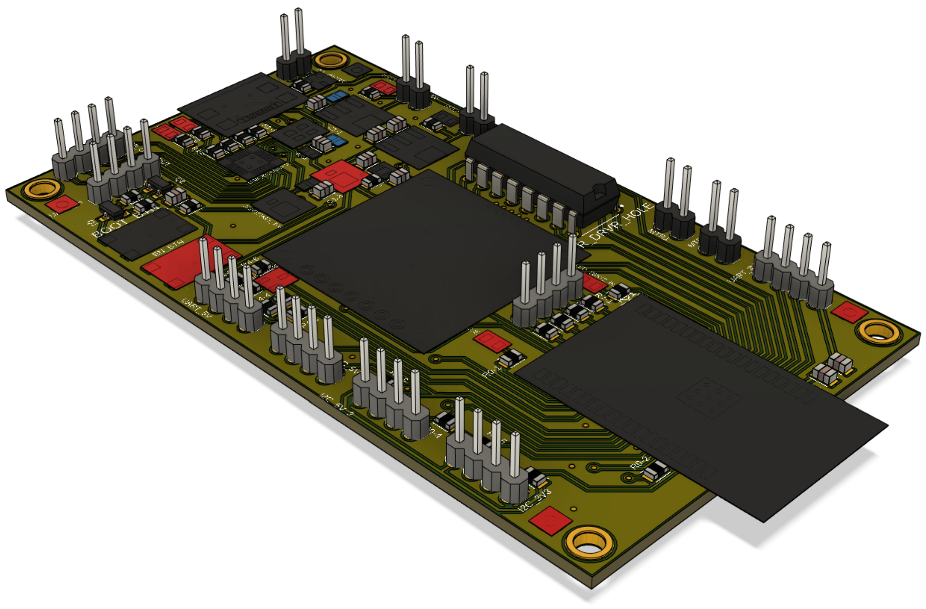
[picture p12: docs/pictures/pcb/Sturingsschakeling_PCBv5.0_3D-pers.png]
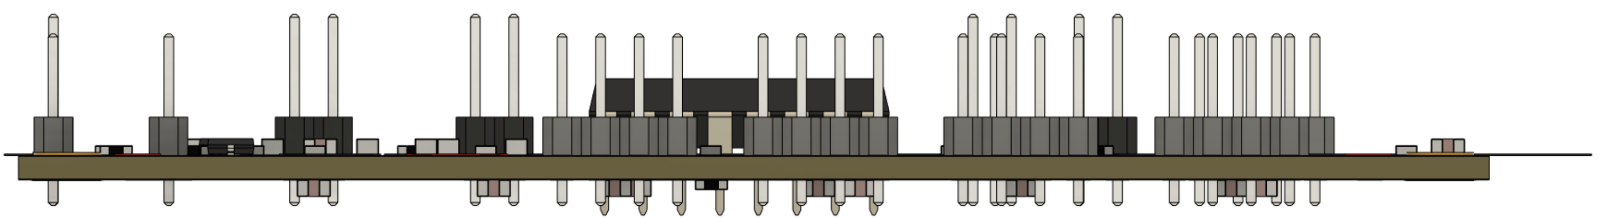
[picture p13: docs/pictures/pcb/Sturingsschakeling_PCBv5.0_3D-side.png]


<iframe src="https://mymsn8893.autodesk360.com/shares/public/SH35dfcQT936092f0e4315df622c6781a3b6?mode=embed" width="1024" height="768" allowfullscreen="true" webkitallowfullscreen="true" mozallowfullscreen="true"  frameborder="0"></iframe>

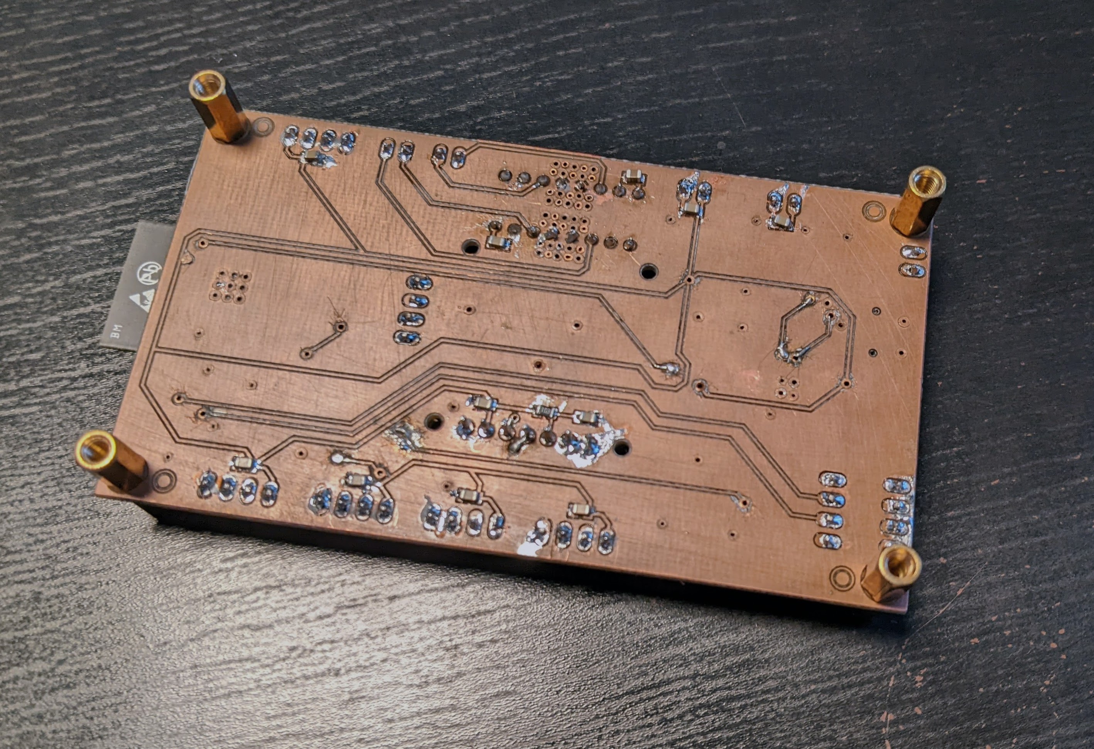
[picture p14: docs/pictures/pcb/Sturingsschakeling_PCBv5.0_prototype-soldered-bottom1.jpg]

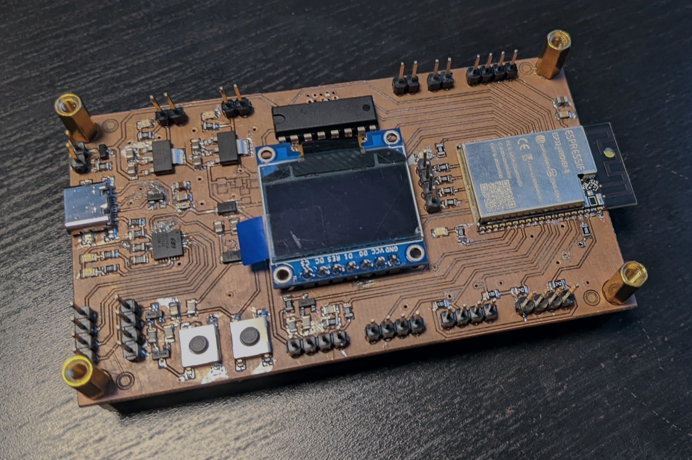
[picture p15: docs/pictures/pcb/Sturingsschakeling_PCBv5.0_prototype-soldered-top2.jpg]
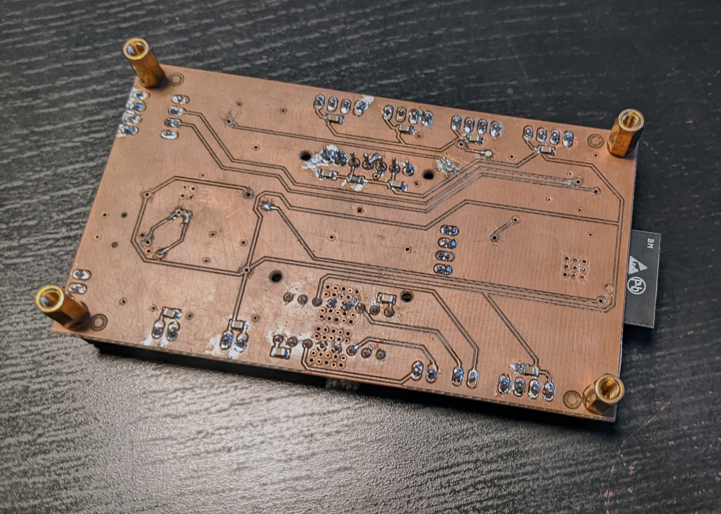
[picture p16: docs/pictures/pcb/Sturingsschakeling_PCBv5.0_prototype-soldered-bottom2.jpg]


### Sensorenschakelingen

#### Sensorenschakeling

Combineerd alle sensoren op één PCB met twee lagen.

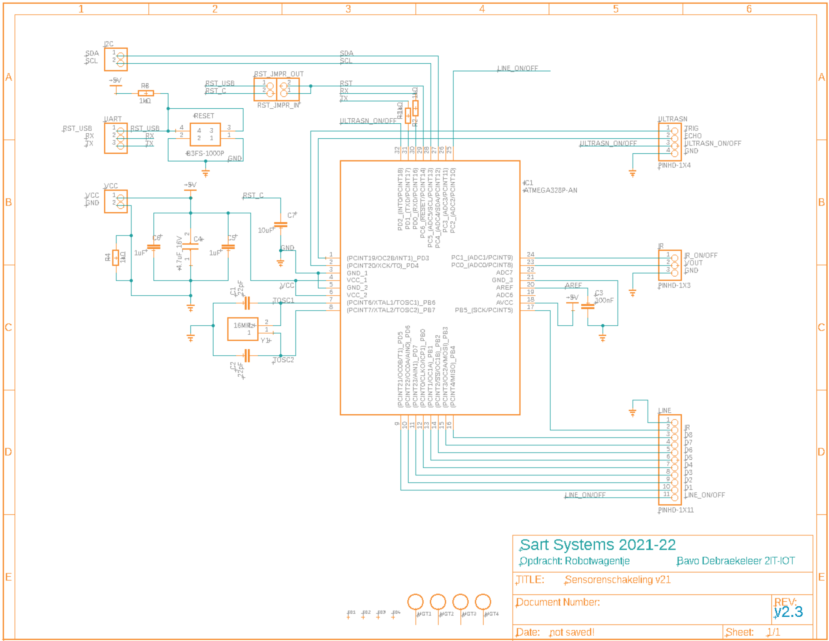
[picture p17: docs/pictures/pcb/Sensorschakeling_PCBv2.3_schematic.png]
<br>
<a href="./pictures/pcb/Sensorenschakeling_schema_v2.3.fsch">Schematic File</a><br>

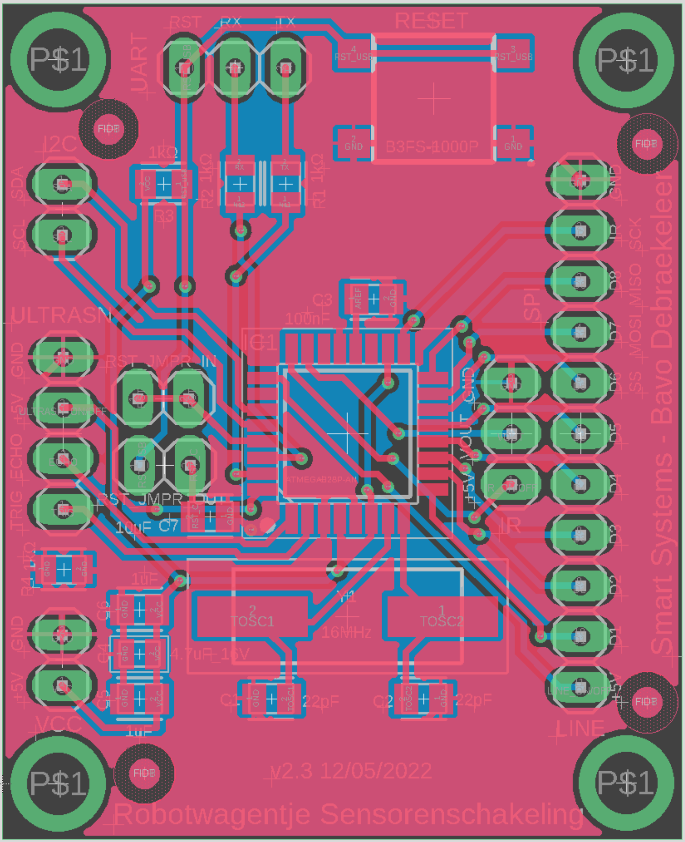
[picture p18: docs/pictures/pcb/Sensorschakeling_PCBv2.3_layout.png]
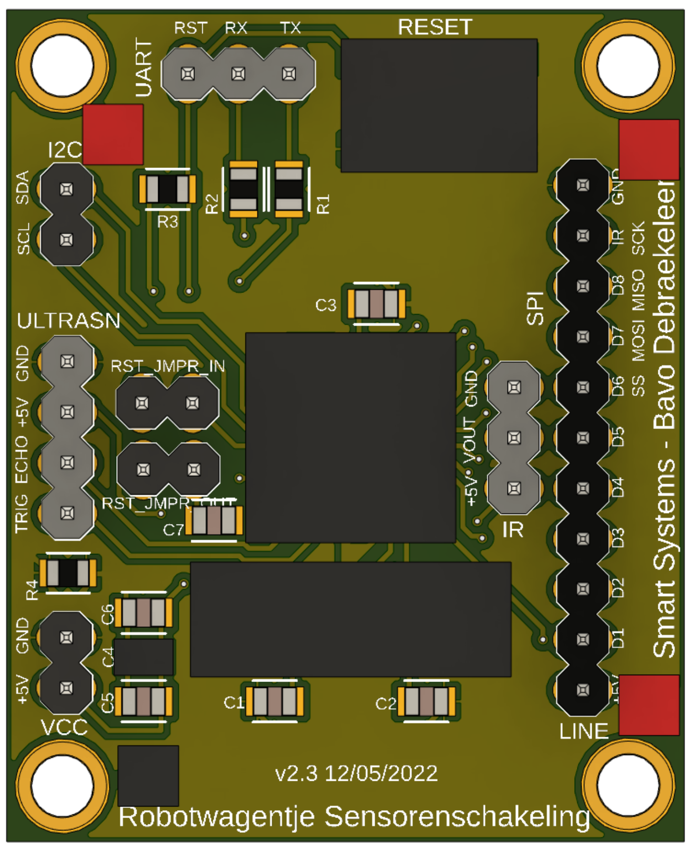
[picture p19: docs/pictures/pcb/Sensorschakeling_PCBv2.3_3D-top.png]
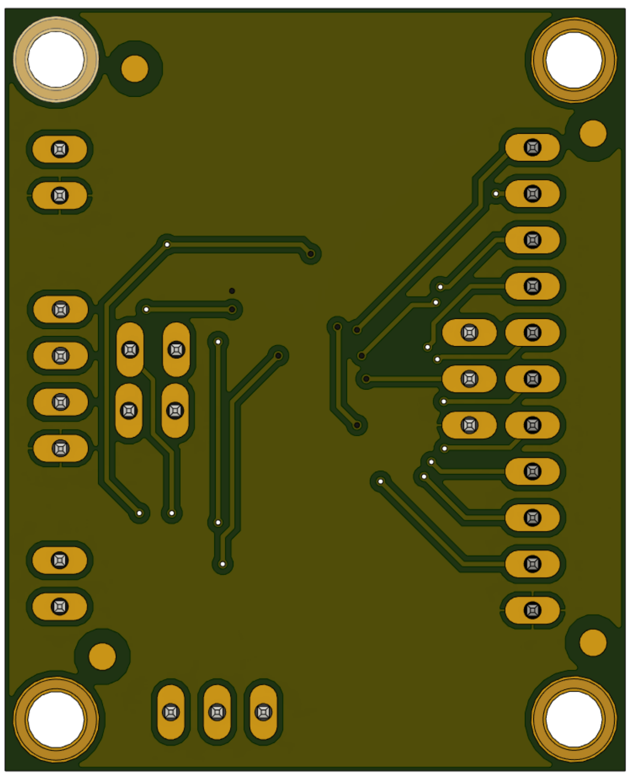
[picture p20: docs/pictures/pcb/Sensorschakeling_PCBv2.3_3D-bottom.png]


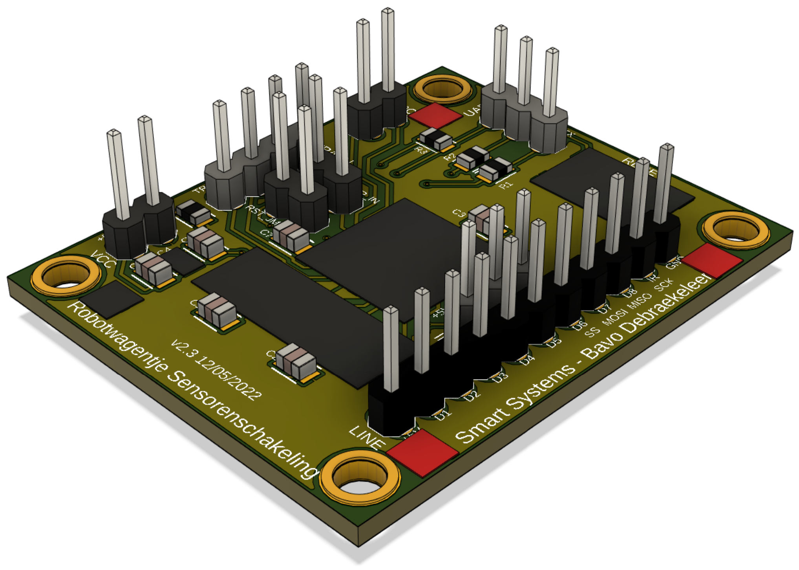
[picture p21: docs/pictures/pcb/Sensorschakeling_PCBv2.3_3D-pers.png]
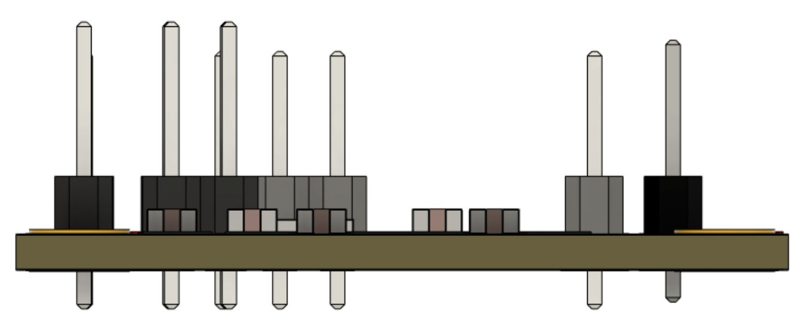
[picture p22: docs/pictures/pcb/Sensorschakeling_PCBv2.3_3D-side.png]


<iframe src="https://mymsn8893.autodesk360.com/shares/public/SH35dfcQT936092f0e43f35af6e629bf74a2?mode=embed" width="1024" height="768" allowfullscreen="true" webkitallowfullscreen="true" mozallowfullscreen="true"  frameborder="0"></iframe>

#### Sensorschakeling - Afstandssensoren

Aparte PCB voor de twee afstandssensoren, zowel IR als Ultrasoon, op één enkele laag.
Voor in-house fabricatie.

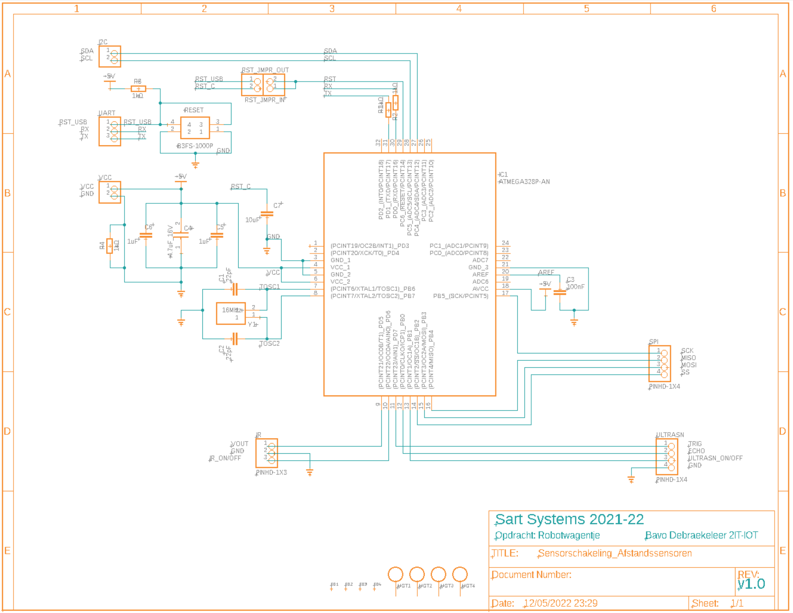
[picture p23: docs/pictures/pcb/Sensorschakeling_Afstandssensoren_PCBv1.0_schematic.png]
<br>
<a href="./pictures/pcb/Sensorschakeling_Afstandssensoren_PCBv1.0.fsch">Schematic File</a><br>

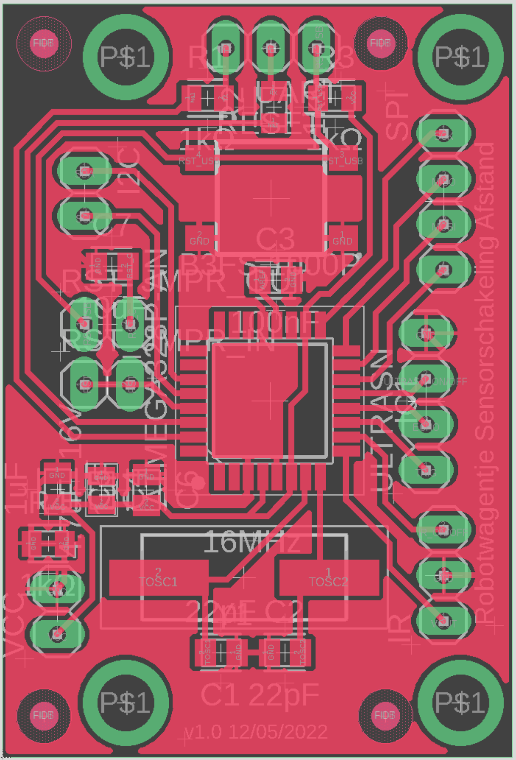
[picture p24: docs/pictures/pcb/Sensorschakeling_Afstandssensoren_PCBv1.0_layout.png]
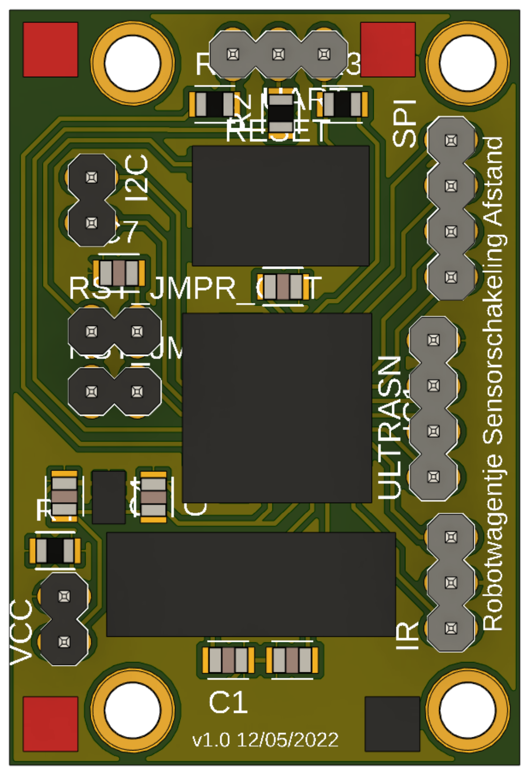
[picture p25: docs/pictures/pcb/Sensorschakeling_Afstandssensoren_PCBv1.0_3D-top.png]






<iframe src="https://mymsn8893.autodesk360.com/shares/public/SH35dfcQT936092f0e4333ed0a33f964ff06?mode=embed" width="1024" height="768" allowfullscreen="true" webkitallowfullscreen="true" mozallowfullscreen="true"  frameborder="0"></iframe>



#### Sensorschakeling - Linetracker

Aparte PCB voor de linetracker module op één enkele laag.
Voor in-house fabricatie.

<br>
<a href="./pictures/pcb/Sensorschakeling_Linetracker_PCBv1.0.fsch">Schematic File</a><br>







<iframe src="https://mymsn8893.autodesk360.com/shares/public/SH35dfcQT936092f0e4323b9fb0bed9636b4?mode=embed" width="1024" height="768" allowfullscreen="true" webkitallowfullscreen="true" mozallowfullscreen="true"  frameborder="0"></iframe>





---

# Software Analyse

## Data I/O



### Sturingsschakeling

<table style="width: 100%">
<colgroup>
    <col span="1" style="width: 20%;">
    <col span="2" style="width: 40%;">
    <col span="3" style="width: 40%;">
</colgroup>
<tr>
    <th>Blok</th>
    <th>Data In</th>
    <th>Data Out</th>
</tr>
<tr>
    <th>ESP32</th>
    <td>
		<li>Configuratie instellingen</li>
		<li>Motor aansturing <b>WiFi</b></li>
		<li>Sensordata <b>I²C</b></li>
	</td>
    <td>
		<li>Feedback data <b>I²C</b></li>
		<li>2x motor aansturing <b>PWM</b></li>
	</td>
</tr>
<tr>
    <td>Motor Driver</td>
    <td>Motor aansturing <b>PWM</b></td>
    <td>N.V.T.</td>
</tr>
<tr>
    <td>OLED Display</td>
    <td>Feedback data <b>I²C</b></td>
    <td>N.V.T.</td>
</tr>
</table>

### Sensorenschakeling Line Tracker

<table style="width: 100%">
<colgroup>
    <col span="1" style="width: 20%;">
    <col span="2" style="width: 40%;">
    <col span="3" style="width: 40%;">
</colgroup>
<tr>
    <th>Blok</th>
    <th>Data In</th>
    <th>Data Out</th>
</tr>
<tr>
    <th>ATMega328p</th>
    <td>
		<li>Configuratie instellingen</li>
		<li>Line Tracker data D1-D8</li>
	</td>
    <td>
		<li>Sensordata <b>I²C</b></li>
		<li>Line Tracker IR aan/uit</li>
	</td>
</tr>
<tr>
	<td>Line tracker</td>
    	<td>IR aan/uit</td>
    	<td>Data van 8x IR sensoren D1-D8.</td>
</table>

### Sensorenschakeling Afstandssensoren

<table style="width: 100%">
<colgroup>
    <col span="1" style="width: 20%;">
    <col span="2" style="width: 40%;">
    <col span="3" style="width: 40%;">
</colgroup>
<tr>
    <th>Blok</th>
    <th>Data In</th>
    <th>Data Out</th>
</tr>
<tr>
    <th>ATMega328p</th>
    <td>
		<li>Configuratie instellingen</li>
		<li>Ultrasoon sensor echo</li>
		<li>IR-afstandssensor afstand als analoge spanning.</li>
	</td>
    <td>
		<li>Sensordata <b>I²C</b></li>
		<li>Ultrasoon sensor trigger</li>
	</td>
</tr>
<tr>
    <td>Ultrasoon sensor</td>
    <td>Trigger</td>
    <td>Echo</td>
</tr>
<tr>
    <td>IR-afstandssensor</td>
    <td>N.V.T.</td>
    <td>Afstand als analoge spanning.</td>
</tr>
</table>

---

## Statediagrams & Flowcharts

<iframe width="1000" height="1000" src="https://miro.com/app/embed/uXjVOCBJkAk=/?pres=1&frameId=3458764527646663194" frameBorder="0" scrolling="no" allowFullScreen></iframe>

### Modus Menu
<br>
 
### Manuele bediening
<br>

### Automatisch rijden
<br>

### Volgens vast patroon rijden
<br>

---

# Release Plan

De planning wordt uitgevoerd in vijf sprints van telkens twee weken.
Elke sprint worden Epics toegewezen die verder zijn opgedeeld in Technical Stories.

## Epics

1. Analyse
2. PCB ontwerp
3. Software ontwikkeling
4. Hardware samenstelling
5. Software implementatie
6. Validatie

---

## Technical Stories

1. Analyse (10 Story Points)
	- <b>Analyse maken</b>
		- Narrative:
			Analyse van de sturingsschakeling volgens onderstaand criteria.
			
		- Acceptance Criteria:
			- Probleemstelling in 2 tot 5 lijnen
			- Mindmap
			- Hardware analyse
			- Hardware blokdiaram
			- Specificatie tabel
			- Argumentatie en alternatieven tabel
			- Software analyse
			- Data In -en Outputs
			- State diagram
			- Flowchart
			- Release plan
			 
		- Story Points (Estimate):
			10

2. PCB ontwerp (10 Story Points)
	- <b>Sturingsschakeling</b>
		- Narrative:
			Het ontwerpen van de hoofd PCB aan de hand van de analyse.
			
		- Acceptance Criteria:
			 - 2x UART connectoren
			 - 3x I²C connectoren
			 - Voltage regulator 5V & 3.3V
			 - Polariteitsbeveiliging
			 - 2x SMD Motor driver
			 - OLED-scherm met I²C-sturing op PCB
			 - Batterij aansluiting (GND, VCC)
			 - Drill holes voor bevestiging van de PCB op het wagentje.
			 - Voldoet aan de vereisten voor in-house fabricatie.
		 
		- Story Points (Estimate):
			5
			
	- <b>Sensorenschakeling</b>
		- Narrative:
			Het ontwerpen van twee dochter PCB's aan de hand van de analyse.<br>
			Eén voor de linetracker en één voor de afstandssensors.<br>
			Deze bevatten een microcontroller die programeerbaar is kan communiceren via I²C.
			
		- Acceptance Criteria:
			- Eén PCB die de data van de Ultrasoon en IR afstandssensoren kan verwerken.
			- Eén PCB die de data van de 8 channel IR Line tracker kan verwerken.
			- Microcontroller die de data kan verwerken en doorsturen via I²C.
			- Drill holes voor bevestiging van de PCB op het wagentje.
			- Voldoet aan de vereisten voor in-house fabricatie.
		 
		- Story Points (Estimate):
			3
			
	- <b>PCB en onderdelen bestellen</b>
		- Narrative:
			Na het ontwerpen moeten de PCB's ook inhouse gefabriceerd worden.<br>
			Verder moet er een Bill of Materials (BOM) gegenereerd worden.<br>
			Componenten moeten verzameld worden en de ontbrekende componenten moeten besteld worden.
			
		- Acceptance Criteria:
			- Elektrische schema's van beide PCB's
			- Board files met de PCB-designs
			- gerber-files van beide PCB's
			- Bill of Materials
			- PCB's fabriceren
			- Ontbrekende componenten bestellen.
		 
		- Story Points (Estimate):
			2

3. Software ontwikkeling (12 Story Points)
	- <b>Menu</b>
		- Narrative:
			De gebruiker moet de software modus kunnen bepalen via een menu met opties aangestuurd via Wifi of Bluetooth.<br>
			Dit menu wordt op het ingebouwde OLED-display weergegeven.
			
		- Acceptance Criteria:
			- Weergeven menu op OLED-display.
			- Modus instellen
			- WiFi en Bluetooth verbinding.
			- Verwerking van commando's volgens statediagram en flowhcart.
		 
		- Story Points (Estimate):
			3
			
	- <b>Manuele bediening</b>
		- Narrative:
			De gebruiker moet het robotwagentje manueel kunnen bedienen.
			De commando's worden via internet of Bluetooth verzonden en via WiFi of Bluetooth ontvangen door de ESP32-module.<br>
			Deze moet de commando's verwerken en de Motor Driver aansturen.
			
		- Acceptance Criteria:
			- Verwerking van commando's volgens statediagram en flowhcart.
			- Aansturen van de motors via de Motor Driver.
		 
		- Story Points (Estimate):
			3
			
	- <b>Automatisch rijden</b>
		- Narrative:
			Het robotwagentje moet automatisch kunnen rijden zonder ergens tegen te botsen.
			Dit gebeurt aan de hand van twee afstandssensors:
			- IR-afstandssensor voor nauwkeurige korte afstand.
			- Ultrasoon sensor voor grove lange afstand.
			
			Wanneer er een obstakel gedetecteerd wordt waarmee het wagentje dreigt te botsen moet het wagentje bijgestuurd worden.<br>
			Het zal blijven draaien, links of rechts, tot er een vrij pad gevonden wordt.<br>
			Waarna het wagentje terug rechtdoor kan rijden.<br>
			Aangezien de sensoren op het dochter PCB staan moet de sensor data gelezen en verwerkt worden met de Arduino Nano/ATMega328p.<br>
			Deze moet dan verzonden worden over I²C naar de ESP23.
			
		- Acceptance Criteria:
			- Modus instellen, van ESP32 naar Arduino sturen over I²C.
			- IR-afstandssensor data opvragen en afstand berekenen met Arduino.
			- Ultrasoon sensor data opvragen en afstand berekenen met Arduino.
			- Data verzonden tussen Arduino en ESP32 met I²C.
			- Obstakel detectie uitvoeren op ESP32.
			- Correcte aansturing van de motor via de Motor Drivers met de ESP32.
		 
		- Story Points (Estimate):
			3
			
	- <b>Volgens vast patroon rijden</b>
		- Narrative:
			Het robotwagentje moet een zwarte lijn kunnen volgen in een bepaald patroon.<br>
			Dit gebeurt aan de hand van een IR Line tracker.<br>
			Als het wagentje afwijkt van de lijn moet er bijgestuurd worden in de juiste richting.<br>
			Het moet ook instaat zijn om een hoek te detecteren en de correcte bocht te nemen.<br>
			Aangezien de sensoren op het dochter PCB staan moet de sensor data gelezen en verwerkt worden met de Arduino Nano/ATMega328p.<br>
			Deze moet dan verzonden worden over I²C naar de ESP23.
			
		- Acceptance Criteria:
			- Modus instellen, van ESP32 naar Arduino sturen over I²C.
			- Patroon in zwarte lijn met absorptie van circa 950 nm.
			- In en uitschakelen van de Line tracker met de Arduino.
			- Line tracker data lezen en verwerken met de Arduino.
			- Data verzonden tussen Arduino en ESP32 met I²C.
			- Correcte aansturing van de motor via de Motor Drivers met de ESP32.
		 
		- Story Points (Estimate):
			3

4. Hardware samenstelling (8 Story Points)
	- <b>3D Print onderdelen</b>
		- Narrative:
			Om het dochter PCB op het wagentje te bevestigen moet een nieuw voorkant ontworpen worden voor het wagentje.<br>
			Hierbij moet er rekening gehouden worden dat de sensors goed geplaatst worden.<br>
			Dit zal gebeuren door de studenten die de minor Maker volgen.
			
		- Acceptance Criteria:
			- Line tracker moet <40 mm van de grond hangen.
			- Geen obstructie voor beide afstandssensoren.
			- USB-poorten van ESP32 en Arduino goed bereikbaar.
		 
		- Story Points (Estimate):
			N/A (Enkel voor studenten van de minor Maker.)
		
	- <b>Hoofd PCB bestukken</b>
		- Narrative:
			Eens de PCB is toegekomen kunnen de componenten gesoldeerd worden.<br>
			De componenten moeten verzameld worden en volgens schema gesoldeerd.
			
		- Acceptance Criteria:
			- Controle PCB print
			- Juiste plaatsing componenten volgens schema.
			- Kwalitatief gesoldeerd.
			- Werkende schakeling bekomen.
		 
		- Story Points (Estimate):
			4
	
	- <b>Dochter PCB's bestukken</b>
		- Narrative:
			Eens de PCB is toegekomen kunnen de componenten gesoldeerd worden.<br>
			De componenten moeten verzameld worden en volgens schema gesoldeerd.
			
		- Acceptance Criteria:
			- Controle PCB print
			- Juiste plaatsing componenten volgens schema.
			- Kwalitatief gesoldeerd.
			- Werkende schakeling bekomen.
		 
		- Story Points (Estimate):
			2
			
	- <b>Robotwagentje samenstellen</b>
		- Narrative:
			Eens de PCB's en 3D prints klaar zijn kan het wagentje in elkaar gestoken worden.
			
		- Acceptance Criteria:
			- Correcte plaatsing van de componenten.
			- Onderdelen met elkaar verbonden waar nodig.
		 
		- Story Points (Estimate):
			2

5. Software implementatie (4 Story Points)
	- <b>Microcontrollers programmeren</b>
		- Narrative:
			Nu de hardware klaar is moet de software nog geprogrammeerd worden op de microcontrollers.
			
		- Acceptance Criteria:
			- Sturingsschakeling geprogrammeerd.
			- Sturingsschakeling geprogrammeerd.
		 
		- Story Points (Estimate):
			4

6. Validatie (6 Story Points)
 	- <b>Hardware testen</b>
 	 	- Narrative:
			Eens de PCB's bestukt zijn moeten deze getest worden op een correcte werking.
			
		- Acceptance Criteria:
			- Alle componenten krijgen de correcte stroomvoorziening en spanning.
			- Microcontrollers werken correct.
			- Inputs en outputs werken.
			- Programmeren van de microcontrollers lukt.
		 
		- Story Points (Estimate):
			2
			
 	- <b>Software testen</b>
 		- Narrative:
			Tijdens de software ontwikkeling worden er unit tests uitgevoerd op de verschillende onderdelen.<br>
			Als alle onderdelen volledig zijn wordt ook de werking samen getest.
			
		- Acceptance Criteria:
			- Sensordata wordt opgemeten.
			- Sensordata wodrt correct verwerkt.
			- Modus instelling werkt.
			- Modussen hebben een correcte werking.
		 
		- Story Points (Estimate):
			2
			
	- <b>Testen geheel</b>
		- Narrative:
			Eens het robotwagentje volledig in elkaar steekt en de software erop staat is het moment van de waarheid aangebroken en zal het moeten getest worden.
			
		- Acceptance Criteria:
			- Alle componenten krijgen de correcte stroomvoorziening en spanning.
			- Microcontrollers werken correct.
			- Sensordata wordt opgemeten.
			- Sensordata wodrt correct verwerkt.
			- Modus instelling werkt.
			- Modussen hebben een correcte werking.
		 
		- Story Points (Estimate):
			2

---

## Sprints

De sprint planning is opgedeeld in vijf sprints van elk twee weken.

1. Analyse & PCB ontwerp (20 Story Points)
2. <em>Afwezig door Internationaal Project: Zanzibar</em>
3. <em>Afwezig door Internationaal Project: Zanzibar</em>
4. Presentatie Analyse & Software ontwikkeling & Hardware samenstelling (20 Story Points)
5. Software implementatie & Validatie (10 Story Points)

<a href="https://www.ap.be/sites/default/files/reglementen/OT/2021-2022/Academische_kalender_21-22_OT.pdf">Academische kalender 2021-22</a><br>

---

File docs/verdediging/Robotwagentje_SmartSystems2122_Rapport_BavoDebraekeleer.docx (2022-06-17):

:::::

Bavo Debraekeleer

2ITIOT

Opdracht voor Smart Systems

Juni 2022 versie 1.0

Robotwagentje

Rapport

# 1 Portfolio en Analyse

Mijn portfolio dat zowel de analyse, pcb ontwerpen en schema’s, de software code, als ook mijn verdediging in de vorm van dit rapport en tussentijdse en examen presentaties, kunnen worden teruggevonden in volgende GitHub repository:

https (https://github.com/BavoDebraekeleer/bavod-robotwagentje-analyse)://github.com/BavoDebraekeleer/ (https://github.com/BavoDebraekeleer/bavod-robotwagentje-analyse)bavod-robotwagentje-analyse (https://github.com/BavoDebraekeleer/bavod-robotwagentje-analyse)

De uitgewerkte analyse kan ook gelezen worden in volgende GitHub Pages pagina:
https://bavodebraekeleer.github.io/bavod-robotwagentje-analyse/ (https://bavodebraekeleer.github.io/bavod-robotwagentje-analyse/)

# 2 Verloop van het project

Dit project is moeizaam verlopen. Door onduidelijkheden en het niet voorradig zijn van vele componenten was het een moeilijke zoektocht naar goede PCB ontwerpen. Deze zijn dan ook door enkele iteraties gegaan. Zeker de PCB voor de ESP32, een module waar ik persoonlijk nog nooit mee gewerkt had, bleek een uitdaging.

Er is uiteraard begonnen met de Analyse, terug te vinden op GitHub (https://bavodebraekeleer.github.io/bavod-robotwagentje-analyse/). Hierin zijn de probleemstelling en systeemspecificaties uitgewerkt. Deze zijn ondersteund door de Hardware en Software Analyse en bevat ook een planning in de vorm van een release plan.

Vervolgens zijn de PCB’s ontworpen. Wanneer deze ontwerpen echter klaar waren om besteld te worden is er overgegaan naar in-house fabricatie. Samen met nog enkele componenten wijzigingen leidde dit tot vertragingen door het nogmaals moeten herontwerpen van de PCB’s. Dit om te voldoen aan de in-house fabricatie vereisten. De software ontwikkeling is hierdoor uitgesteld en heeft enorme vertraging opgelopen.

Na het bestukken van de PCB’s bleek vervolgens dat deze niet werken. Bij de sensorschakelingen gaat het vermoedelijk over componenten die beschadigd zijn geraakt tijdens het solderen. Bij de sturingsschakeling is er vermoedelijk een kortsluiting. Zie hoofdstuk metingen voor verdere verduidelijking. Er was echter geen tijd meer om deze goed te analyseren en nieuwe versies te ontwerpen en fabriceren.

Kortom een zeer moeizaam verloop met geen werkend resultaat, maar wel een zeer leerrijk proces. Ik heb leren schakelingen voor microcontrollers op te bouwen aan de hand van datasheets. Ook over het ontwerpen van PCB’s heb ik nog veel bijgeleerd, en natuurlijk de in-house fabricatie voor prototyping.

# 3 Resultaten

Het resultaat van dit project is:

- uitgebreide analyse
- schakeling en PCB ontwerpen
- bestukte PCB prototypes aan de hand van in-house fabricatie
- een eerste opbouw van de onderdelen van de embeded software


# 4 Metingen

Aangezien de bestukte PCB’s niet werken valt er niet veel te meten.

## 4.1 Sturingsschakeling

Uitgevoerde metingen:

- Alle paden en via’s zijn tijdens en na het solderen na gemeten op juiste verbindingen. Dit was allemaal in orde. Uitzondering hierbij is de USB interface en USB-poort waarbij het zeer moeilijk is om na te gaan wat er onder de IC gebeurt.
- De voedingslijnen zijn opgemeten bij connectie met USB-poort en afzonderlijke batterij voeding. De USB-poort geeft echter geen voeding, meting is 0V, en de afzonderlijke voeding geeft een zeer lage spanning, ongeveer 0.5V. Er is dus ergens verlies in de schakeling. Na de 5V voltage regulator is er echter geen spanning, maar na de 3.3V, die achter de 5V is geschakeld, is er weer wel een kleine spanning.

## 4.2 Sensorschakelingen

Uitgevoerde metingen op beide PCB’s:

- Alle paden hebben de correcte connecties. Geen kortsluitingen.
- Voeding op de 5V pin werkt en komt tot aan de microcontroller.
- Bij poging tot programmeren van de bootloader op de microcontroller met SPI komt er geen respons. Ook op de kloklijnen is er geen activiteit. Vermoedelijk is de microcontroller beschadigd, of de externe klok werkt niet, of de klok moet nog worden ingesteld via het programmeren, maar dit gaat dus niet.

# 5 Conclusie

Ik heb extra ervaring opgedaan en ook zeer veel bijgeleerd in dit OLOD.

- Mijn analyse vaardigheden zijn verder uitgebreid.
- Ik heb geleerd om verschillende microcontrollers in een eigen ontworpen schakeling te integreren en wat hierbij komt kijken.
- Mijn PCB ontwerp vaardigheden zijn gegroeid door het werken met meerdere lagen en via’s, als ook zelf footprints maken en aanpassen in Fusion 360.
- Ik heb geleerd een PCB ontwerp te maken voor in-house fabricatie en de fabricatie zelf.
- Een inleiding tot pick-and-place machine, maar jammer genoeg niet meer kunnen gebruiken.
- Beter leren solderen van SMD componenten met soldeerpasta.

Jammer genoeg is er ook heel wat fout gelopen. Zo werken de bestukte PCB’s niet en is de embeded software niet volledig. Bij gevolg is het programmeren van de microcontrollers dus ook niet gelukt. Zelf de bootloader op de ATMega zetten werkte niet.

Ik heb dus zeker wel veel bijgeleerd en ben ervan overtuigd dat met betere communicatie en een correcte planning dit een succes was geweest.

Robotwagentje Rapport Smart Systems

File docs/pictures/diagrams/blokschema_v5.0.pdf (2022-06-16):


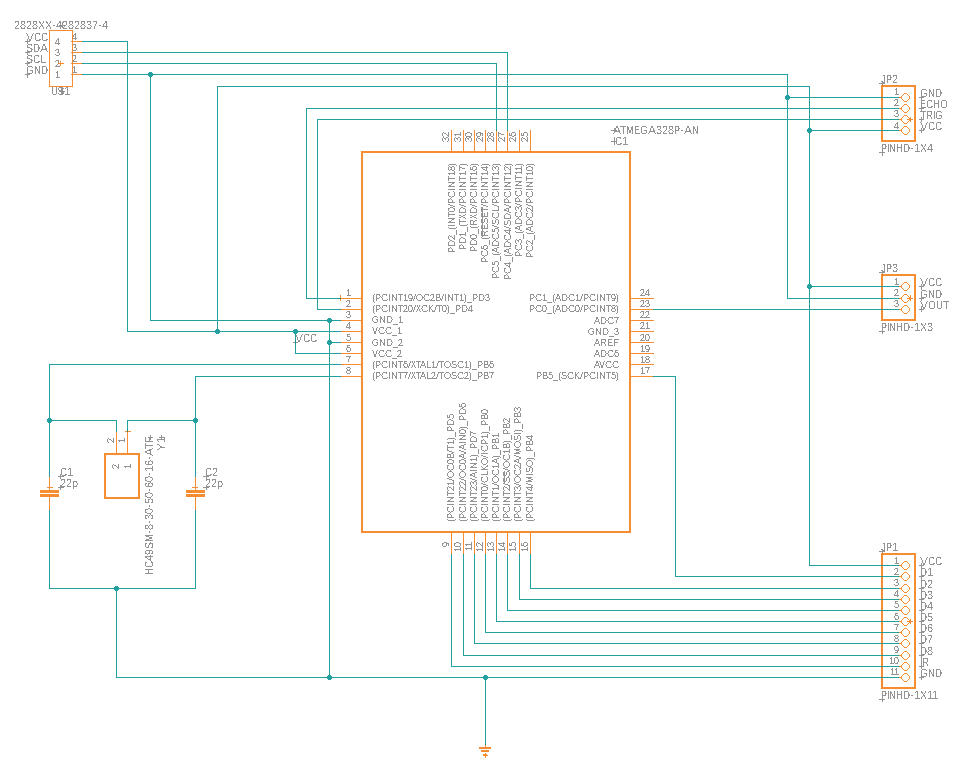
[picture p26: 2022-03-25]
docs/pictures/pcb/Sensorschakeling_PCBv1.0_schematic.png

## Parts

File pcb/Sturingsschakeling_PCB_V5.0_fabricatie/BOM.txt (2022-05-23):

Partlist exported from Team Hub: Bavo   Project: Smart Systems - Robotwagentje  Board: Sturingsschakeling_Inhouse_main v30 at 22/05/2022 21:31

Qty Value                         Device                        Package                       Parts                                                                           Description                                                                                                                                     ARROW_PART_NUMBER   ARROW_PRICE-STOCK                                                             BOM CATEGORY            DESCRIPTION                                                                                                      HEIGHT           MANUFACTURER                                     MANUFACTURER_NAME                 MANUFACTURER_PART_NUMBER    MOUSER_PART_NUMBER             MOUSER_PRICE-STOCK                                                                                                MPN                OPERATING_TEMP      PART_STATUS                                                                                 POPULARITY                                                                                              RATING                                                                                                ROHS_COMPLIANT       SERIES                                                                                             SUB-CATEGORY SUB_CATEGORY THERMALLOSS TOLERANCE TYPE VOLTAGE_RATING
6   100nF                         C_CHIP-0805(2012-METRIC)      CAPC2012X110                  C0-2, C1-2, C1-4, C2-3, C3-1, C3-2                                              Capacitor - Generic                                                                                                                                                                                                                                   Capacitor                                                                                                                                                                                                                                                                                                                                                                                                                                                                                                                                                                                                                                                                                                                                                                                                                                                                                                                                                         
4   100Ω                          R_CHIP-0805(2012-METRIC)      RESC2012X65                   R7-1, R7-2, R7-3, R7-4                                                          Resistor Fixed - Generic                                                                                                                                                                                                                              Resistor                                                                                                                                                                                                                                                                                                                                                                                                                                                                                                                                                                                                                                                                                                                                                                                                                                                                                       Fixed                                                              
7   10kΩ                          R_CHIP-0805(2012-METRIC)      RESC2012X65                   R1-4, R3-1, R4-4, R4-6, R6-1, R6-2, R6-3                                        Resistor Fixed - Generic                                                                                                                                                                                                                              Resistor                                                                                                                                                                                                                                                                                                                                                                                                                                                                                                                                                                                                                                                                                                                                                                                                                                                                                       Fixed                                                              
6   150080RS75000                 150080RS75000                 LEDC2012X80N                  LED_3V3_GRN, LED_5V_GRN, LED_RX_RED, LED_TEST1_BLUE, LED_TEST2_BLUE, LED_TX_GRN LED,Wurth Elektronik,150080RS75000 Wurth Elektronik 150080RS75000, WL-SMCW Series Red LED, 625 nm 2012 (0805) Clear, Rectangle Lens SMD package                                                                                                                           LED                                                                                                              Wurth Elektronik 150080RS75000 Wurth Elektronik 150080RS75000      WL-SMCW Series Red LED            625 nm 2012 (0805) Clear    Rectangle Lens SMD package    0.8mm                                                                                                                                Wurth Elektronik    150080RS75000                                                                               710-150080RS75000                                                                                       https://www.mouser.co.uk/ProductDetail/Wurth-Elektronik/150080RS75000?qs=LlUlMxKIyB2jdCo7bnfgew%3D%3D                                                                                                                                                                                            
11  1kΩ                           R_CHIP-0805(2012-METRIC)      RESC2012X65                   R0-1, R0-7, R0-8, R1-3, R1-5, R1-6, R4-1, R4-2, R4-3, R5-1, R5-2                Resistor Fixed - Generic                                                                                                                                                                                                                              Resistor                                                                                                                                                                                                                                                                                                                                                                                                                                                                                                                                                                                                                                                                                                                                                                                                                                                                                       Fixed                                                              
11  1uF                           C_CHIP-0805(2012-METRIC)      CAPC2012X110                  C2-4, C5-2, C5-4, C6-1, C7-1, C7-2, C7-3, C7-4, C7-5, C7-6, C7-7                Capacitor - Generic                                                                                                                                                                                                                                   Capacitor                                                                                                                                                                                                                                                                                                                                                                                                                                                                                                                                                                                                                                                                                                                                                                                                                                                                                                                                                         
1   22k1Ω                         R_CHIP-0805(2012-METRIC)      RESC2012X65                   R1-1                                                                            Resistor Fixed - Generic                                                                                                                                                                                                                              Resistor                                                                                                                                                                                                                                                                                                                                                                                                                                                                                                                                                                                                                                                                                                                                                                                                                                                                                       Fixed                                                              
1   22uF                          C_CHIP-0805(2012-METRIC)      CAPC2012X110                  C0-1                                                                            Capacitor - Generic                                                                                                                                                                                                                                   Capacitor                                                                                                                                                                                                                                                                                                                                                                                                                                                                                                                                                                                                                                                                                                                                                                                                                                                                                                                                                         
2   2k4Ω                          R_CHIP-0805(2012-METRIC)      RESC2012X65                   R0-5, R0-6                                                                      Resistor Fixed - Generic                                                                                                                                                                                                                              Resistor                                                                                                                                                                                                                                                                                                                                                                                                                                                                                                                                                                                                                                                                                                                                                                                                                                                                                       Fixed                                                              
1   4.7uF                         C_CHIP-0805(2012-METRIC)      CAPC2012X110                  C5-3                                                                            Capacitor - Generic                                                                                                                                                                                                                                   Capacitor                                                                                                                                                                                                                                                                                                                                                                                                                                                                                                                                                                                                                                                                                                                                                                                                                                                                                                                                                         
3   4.7uF_16V                     CC0805ZKY5V7BB475             CAPC2012X145N                 C1-1, C1-3, C5-1                                                                YAGEO - CC0805ZKY5V7BB475 - SMD Multilayer Ceramic Capacitor, 4.7 F, 16 V, 0805 [2012 Metric], +80%, -20%, Y5V, CC Series                       CC0805ZKY5V7BB475   https://www.arrow.com/en/products/cc0805zky5v7bb475/yageo                                             YAGEO - CC0805ZKY5V7BB475 - SMD Multilayer Ceramic Capacitor                                                      4.7 F            16 V                                             0805 [2012 Metric]                +80%                        -20%                           Y5V                                                                                                               CC Series         1.45mm                                                                                                          KEMET                                                                                                   CC0805ZKY5V7BB475                                                                                     603-CC805ZKY5V7BB475 https://www.mouser.co.uk/ProductDetail/Yageo/CC0805ZKY5V7BB475?qs=7s%252B3O6pAiyA4wtTM471wUA%3D%3D                                                                    
1   47k5Ω                         R_CHIP-0805(2012-METRIC)      RESC2012X65                   R1-2                                                                            Resistor Fixed - Generic                                                                                                                                                                                                                              Resistor                                                                                                                                                                                                                                                                                                                                                                                                                                                                                                                                                                                                                                                                                                                                                                                                                                                                                       Fixed                                                              
1   499Ω                          R_CHIP-0805(2012-METRIC)      RESC2012X65                   R0-2                                                                            Resistor Fixed - Generic                                                                                                                                                                                                                              Resistor                                                                                                                                                                                                                                                                                                                                                                                                                                                                                                                                                                                                                                                                                                                                                                                                                                                                                       Fixed                                                              
3   4k7Ω                          R_CHIP-0805(2012-METRIC)      RESC2012X65                   R0-3, R0-4, R4-5                                                                Resistor Fixed - Generic                                                                                                                                                                                                                              Resistor                                                                                                                                                                                                                                                                                                                                                                                                                                                                                                                                                                                                                                                                                                                                                                                                                                                                                       Fixed                                                              
2   B3FS-1000P                    B3FS-1000P                    B3FS-1000P                    BOOT_BTN, EN_BTN                                                                Switch Tact,6x6mm,flat act,gen purp,tape Plunger Tactile Switch, SPST-NO 0.05 A@ 24 V dc 0.5mm                                                  B3FS-1000P          https://www.arrow.com/en/products/b3fs-1000p/omron?region=nac                                         Switch Tact                                                                                                      6x6mm            flat act                                         gen purp                          tape Plunger Tactile Switch  SPST-NO 0.05 A@ 24 V dc 0.5mm mm                                                                                                                                   Omron Electronics   B3FS-1000P                                                                                  653-B3FS-1000P                                                                                          https://www.mouser.co.uk/ProductDetail/Omron-Electronics/B3FS-1000P?qs=ImaqFqjHA4k6odVF2%2FXWpQ%3D%3D                                                                                                                                                                                            
2   BC817-16SMD                   BC817-16SMD                   SOT23-BEC                     Q1, Q2                                                                          NPN Transistor                                                                                                                                                                                                                                                                                                                                                                                                                                                                                                                                                                                                                                                                                                                                                                                                 0                                                                                                                                                                                                                                                                                                                                                                                                        
4   BEAGLEBONEBLACK_MOUNTING_HOLE BEAGLEBONEBLACK_MOUNTING_HOLE BEAGLEBONEBLACK_MOUNTING_HOLE MGT1, MGT2, MGT3, MGT4                                                          Chassis Mounting Hole w/GND connection ability                                                                                                                                                                                                                                                                                                                                                                                                                                                                                                                                                                                                                                                                                                                                                                                                                                                                                                                                                                                                                                                                                                                                                                          
1   CP2102N-A02-GQFN28R           CP2102N-A02-GQFN28R           QFN50P500X500X80-29N          USB_INTERFACE                                                                   USB Interface IC USB to UART bridge - QFN28                                                                                                     CP2102N-A02-GQFN28R https://www.arrow.com/en/products/cp2102n-a02-gqfn28r/silicon-labs?region=nac                         USB Interface IC USB to UART bridge - QFN28                                                                      0.8mm                                                             Silicon Labs                      CP2102N-A02-GQFN28R         634-CP2102NA02QFN28R           https://www.mouser.co.uk/ProductDetail/Silicon-Labs/CP2102N-A02-GQFN28R?qs=u16ybLDytRag4qKvSH3fTw%3D%3D                                                                                                                                                                                                                                                                                                                                                                                                                                                                                                                                                       
2   DMG3414U                      DMG3414U                      SOT96P240X110-3N              LVL_SHFT_N-MOSFET, POL_PROTEC                                                   DIODES INC. - DMG3414U - MOSFET, N CH, W DIODE, 20V, 4.2A, SOT23                                                                                                                                                                                                          DIODES INC. - DMG3414U - MOSFET                                                                                   N CH             W DIODE                                          20V                               4.2A                        SOT23                         1.1mm                                                                                                                                Diodes Inc.         DMG3414U                                                                                    N/A                                                                                                     https://www.mouser.co.uk/ProductDetail/Diodes-Incorporated/DMG3414U?qs=Ledwo0gu0jiKJ4xsXSUnyQ%3D%3D                                                                                                                                                                                              
1   ESP32-WROVER                  ESP32-WROVER                  ESP32WROVER                   IC1                                                                             WiFi Modules (802.11) SMD Module, ESP32-D0WDQ6, 64Mbits PSRAM, 32Mbits SPI flash, PCB Antenna                                                                                                                                                                             WiFi Modules (802.11) SMD Module                                                                                  ESP32-D0WDQ6     64Mbits PSRAM                                    32Mbits SPI flash                 PCB Antenna                3mm                                                                                                                                              Espressif Systems  ESP32-WROVER        356-ESP32-WROVER                                                                                                                                                                                                                                                                                                                                                                                                                                                                                     
4   FID_60MIL_P                   FID_60MIL_P                   FID_060_P                     FD1, FD2, FD3, FD4                                                              Fiducial marks. Top and Bottom copper with stop mask
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

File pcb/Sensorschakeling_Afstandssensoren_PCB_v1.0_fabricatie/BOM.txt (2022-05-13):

Partlist exported from Team Hub: Bavo   Project: Smart Systems - Robotwagentje  Board: Sensorschakeling_Afstandssensoren v9 at 13/05/2022 0:10

Qty Value                         Device                        Package                       Parts                               Description                                                                                                               ARROW_PART_NUMBER ARROW_PRICE-STOCK                                                               BOM CATEGORY  DESCRIPTION                                                  HEIGHT                    MANUFACTURER MANUFACTURER_NAME   MANUFACTURER_PART_NUMBER    MOUSER_PART_NUMBER             MOUSER_PRICE-STOCK MPN                      OPERATING_TEMP    PART_STATUS       POPULARITY                                                                                                      RATING                                                                                                ROHS_COMPLIANT       SERIES                                                                                             SUB-CATEGORY THERMALLOSS TOLERANCE TYPE VOLTAGE_RATING
4                                 PINHD-1X2                     1X02                          I2C, RST_JMPR_IN, RST_JMPR_OUT, VCC PIN HEADER                                                                                                                                                                                                                                                                                                                                                                                                                                                                                                   98                                                                                                                                                                                                                                                                                                                                                                                                  
1                                 PINHD-1X3                     1X03                          UART                                PIN HEADER                                                                                                                                                                                                                                                                                                                                                                                                                                                                                                   92                                                                                                                                                                                                                                                                                                                                                                                                  
1   100nF                         C_CHIP-0805(2012-METRIC)      CAPC2012X110                  C3                                  Capacitor - Generic                                                                                                                                                                                                             Capacitor                                                                                                                                                                                                                                                                                                                                                                                                                                                                                                                                                                                                                                                                        
1   10uF                          C_CHIP-0805(2012-METRIC)      CAPC2012X110                  C7                                  Capacitor - Generic                                                                                                                                                                                                             Capacitor                                                                                                                                                                                                                                                                                                                                                                                                                                                                                                                                                                                                                                                                        
1   16MHz                         HC49SM-8-30-50-60-16-ATF      HC49SM830506016ATF            Y1                                  MULTICOMP - HC49SM-8-30-50-60-16-ATF - CRYSTAL, 8MHZ, 16PF, SMD                                                                                                                                                                           MULTICOMP - HC49SM-8-30-50-60-16-ATF - CRYSTAL                8MHZ                      16PF         SMD                4mm                                                        MULTICOMP          HC49SM-8-30-50-60-16-ATF                                                                                                                                                                                                                                                                                                                                                                                                                                         
4   1kΩ                           R_CHIP-0805(2012-METRIC)      RESC2012X65                   R1, R2, R3, R4                      Resistor Fixed - Generic                                                                                                                                                                                                        Resistor                                                                                                                                                                                                                                                                                                                                                                                                                                                                                                                                                                                                                   Fixed                                                 
2   1uF                           C_CHIP-0805(2012-METRIC)      CAPC2012X110                  C5, C6                              Capacitor - Generic                                                                                                                                                                                                             Capacitor                                                                                                                                                                                                                                                                                                                                                                                                                                                                                                                                                                                                                                                                        
2   22pF                          C_CHIP-0805(2012-METRIC)      CAPC2012X110                  C1, C2                              Capacitor - Generic                                                                                                                                                                                                             Capacitor                                                                                                                                                                                                                                                                                                                                                                                                                                                                                                                                                                                                                                                                        
1   4.7uF_16V                     CC0805ZKY5V7BB475             CAPC2012X145N                 C4                                  YAGEO - CC0805ZKY5V7BB475 - SMD Multilayer Ceramic Capacitor, 4.7 F, 16 V, 0805 [2012 Metric], +80%, -20%, Y5V, CC Series CC0805ZKY5V7BB475 https://www.arrow.com/en/products/cc0805zky5v7bb475/yageo                                     YAGEO - CC0805ZKY5V7BB475 - SMD Multilayer Ceramic Capacitor  4.7 F                     16 V         0805 [2012 Metric]  +80%                        -20%                           Y5V                CC Series               1.45mm                              KEMET                                                                                                           CC0805ZKY5V7BB475                                                                                     603-CC805ZKY5V7BB475 https://www.mouser.co.uk/ProductDetail/Yageo/CC0805ZKY5V7BB475?qs=7s%252B3O6pAiyA4wtTM471wUA%3D%3D                                                       
1   ATMEGA328P-AN                 ATMEGA328P-AN                 QFP80P900X900X120-32N         IC1                                 MCU 8-bit ATmega AVR RISC 32KB Flash Atmel ATMEGA328P-AN, 8bit AVR Microcontroller, 20MHz, 32 kB Flash, 32-Pin TQFP       ATMEGA328P-AN     https://www.arrow.com/en/products/atmega328p-an/microchip-technology?region=nac               MCU 8-bit ATmega AVR RISC 32KB Flash Atmel ATMEGA328P-AN      8bit AVR Microcontroller  20MHz        32 kB Flash         32-Pin TQFP                1.2mm                                             Microchip                ATMEGA328P-AN     556-ATMEGA328P-AN https://www.mouser.co.uk/ProductDetail/Microchip-Technology-Atmel/ATMEGA328P-AN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                                                                                                                                                                                                                                                                                     
1   B3FS-1000P                    B3FS-1000P                    B3FS-1000P                    RESET                               Switch Tact,6x6mm,flat act,gen purp,tape Plunger Tactile Switch, SPST-NO 0.05 A@ 24 V dc 0.5mm                            B3FS-1000P        https://www.arrow.com/en/products/b3fs-1000p/omron?region=nac                                 Switch Tact                                                  6x6mm                     flat act     gen purp            tape Plunger Tactile Switch  SPST-NO 0.05 A@ 24 V dc 0.5mm mm                                          Omron Electronics B3FS-1000P        653-B3FS-1000P                                                                                                  https://www.mouser.co.uk/ProductDetail/Omron-Electronics/B3FS-1000P?qs=ImaqFqjHA4k6odVF2%2FXWpQ%3D%3D                                                                                                                                                                               
4   BEAGLEBONEBLACK_MOUNTING_HOLE BEAGLEBONEBLACK_MOUNTING_HOLE BEAGLEBONEBLACK_MOUNTING_HOLE MGT1, MGT2, MGT3, MGT4              Chassis Mounting Hole w/GND connection ability                                                                                                                                                                                                                                                                                                                                                                                                                                                                                                                                                                                                                                                                                                                                                                                                                                                                   
4   FID_60MIL_P                   FID_60MIL_P                   FID_060_P                     FD1, FD2, FD3, FD4                  Fiducial marks. Top and Bottom copper with stop mask                                                                                                                                                                                                                                                                                                                                                                                                                                                                                                                                                                                                                                                                                                                                                                                                                                                             
1   PINHD-1X3                     PINHD-1X3                     1X03                          IR                                  PIN HEADER                                                                                                                                                                                                                      CONNECTOR                                                                                                                                                                                                                                                                                                                                                                                                                                                                                                                                                                                                                  PIN-HEADER                                            
2   PINHD-1X4                     PINHD-1X4                     1X04                          SPI, ULTRASN                        PIN HEADER                                                                                                                                                                                                                      CONNECTOR                                                                                                                                                                                                                                                                                                                                                                                                                                                                                                                                                                                                                  PIN-HEADER

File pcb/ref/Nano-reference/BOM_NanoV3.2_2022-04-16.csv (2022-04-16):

ID | Name | Designator | Footprint | Quantity | Manufacturer Part | Manufacturer | Supplier | Supplier Part | Price
1 | 100nF | C1,C4,C9,C6 | C0603-ROUND`value`100nF | 4
2 | 1uF | C3,C7,C8 | C0603-ROUND`value`1uF | 3
3 | 1K | RP1,RP2 | CAY16`value`1K | 2
4 | DNP | U$53,U$54,U$4,U$5 | FD-1-1.5`value`DNP | 4
5 | FT232RL | IC1 | SSOP28`value`FT232RL | 1
6 | MFFSMF050 | F1 | 0603-1608X90N`value`MFFSMF050 | 1
7 | 4,7uF_16V | C5,C2 | TAN-A`value`4,7uF_16V | 2
8 | LM1117IMPX-5.0 | IC2 | LINEAR_SOT223`value`LM1117IMPX-5.0 | 1
9 | SS1P3L | D1 | DO220AAL`value`SS1P3L | 1
10 | RESET | SW1 | SMD_157SW`value`RESET | 1
11 | _ | J3 | USB-MINI-B_2`value` | 1
12 | 16MHz | Y1 | RESONATOR`value`16MHz | 1
13 | XXXX_STRIPNANO | J1,J2 | HEAD15-NOSS`value`XXXX_STRIPNANO | 2
14 | _ | J4 | 2X03`value` | 1
15 | Red | RX | CHIPLED_0805`value`Red | 1
16 | Green | TX,PWR | CHIPLED_0805`value`Green | 2
17 | Yellow | L | CHIPLED_0805`value`Yellow | 1
18 | ATMEGA328P-AU | IC3 | TQFP32-08`value`ATMEGA328P-AU | 1
19 | DNP | D-,D+ | TP-1.00MM`value`DNP | 2

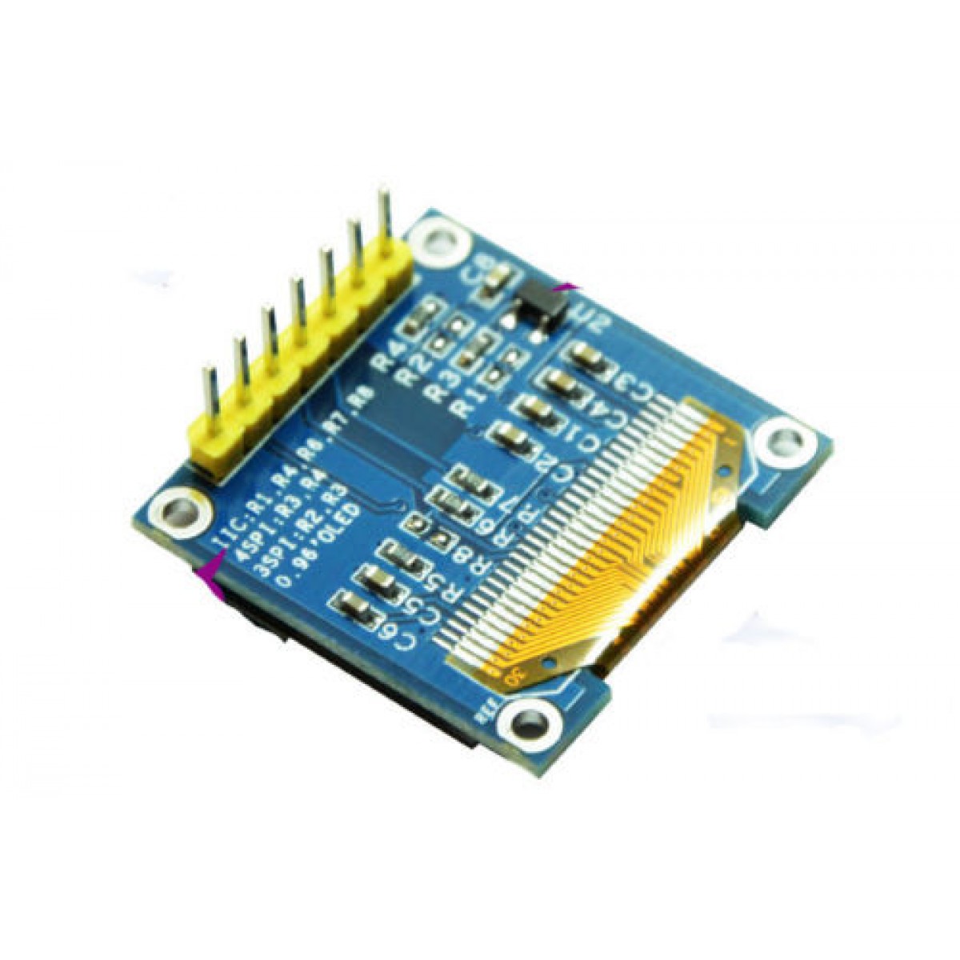
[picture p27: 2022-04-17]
docs/pictures/components/0.96_oled_back.jpg

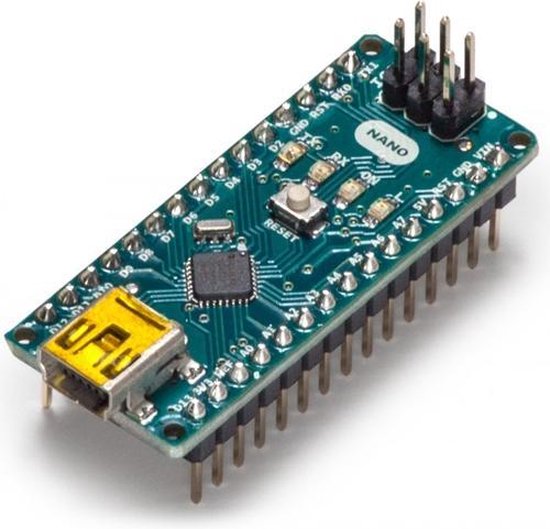
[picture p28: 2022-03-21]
docs/pictures/components/Arduino_Nano.jpg

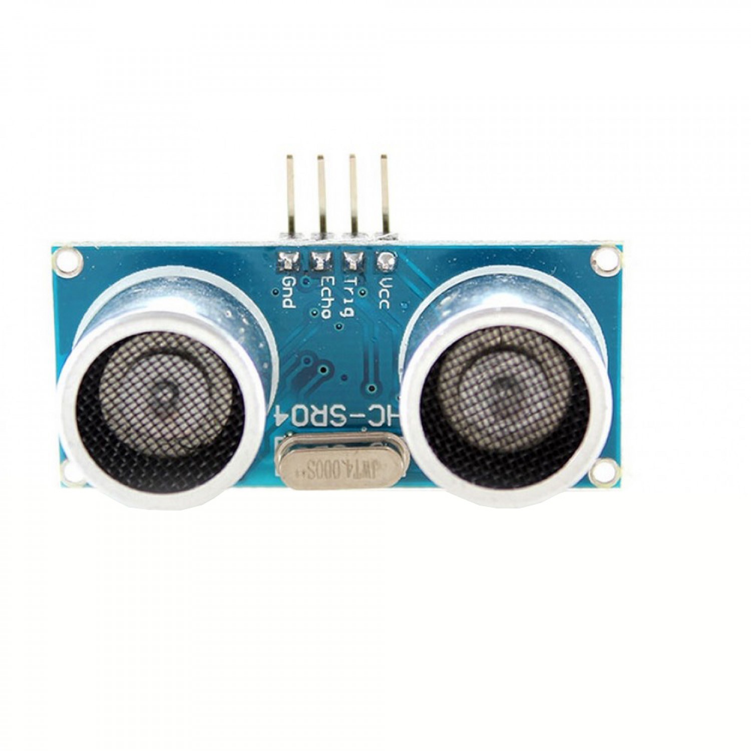
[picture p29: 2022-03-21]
docs/pictures/components/HC-SR04_front.jpg

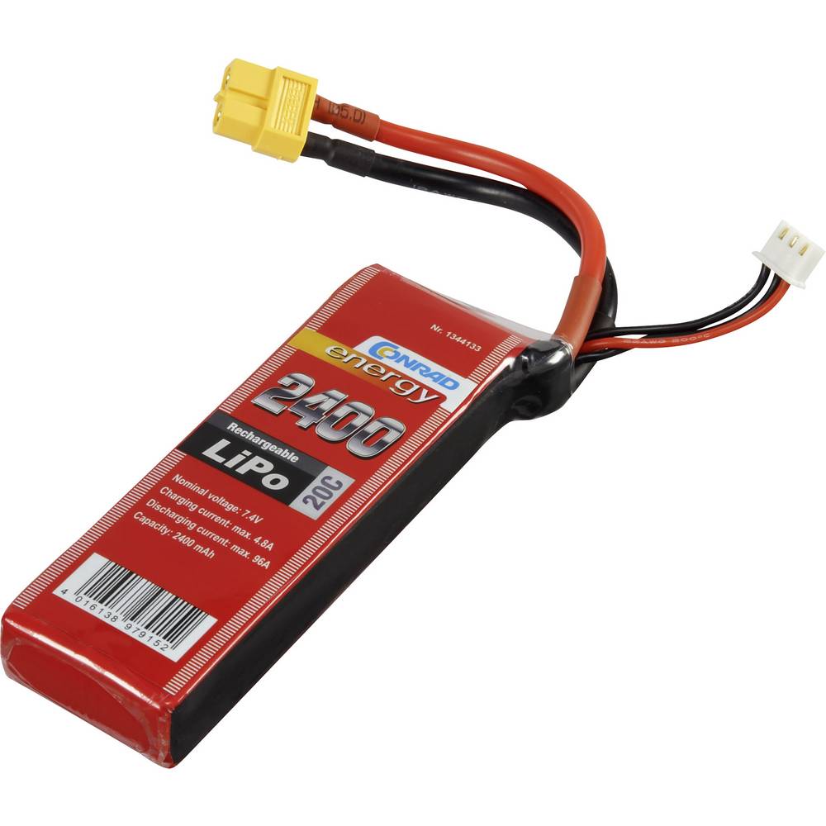
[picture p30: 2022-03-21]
docs/pictures/components/accu.jpg

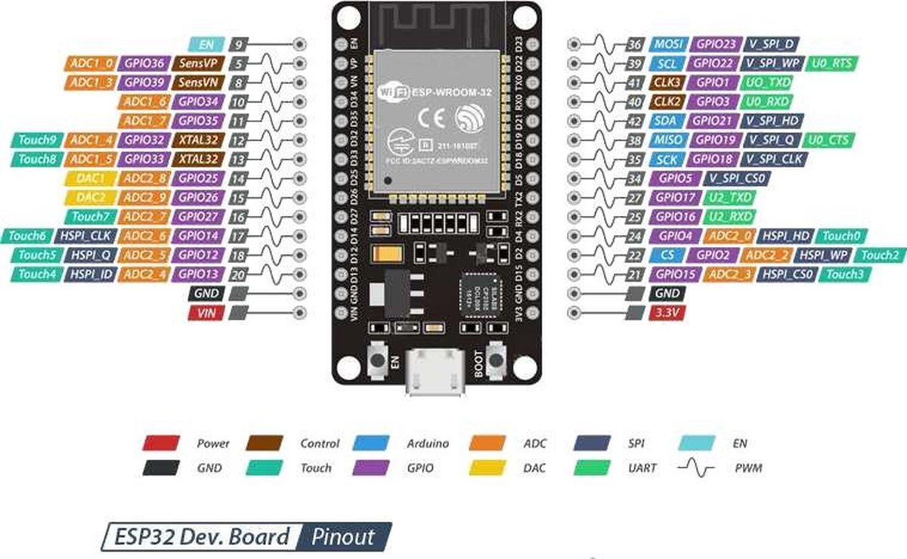
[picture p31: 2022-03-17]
docs/pictures/components/ESP_WROOM_32_DevKit_pins.jpg

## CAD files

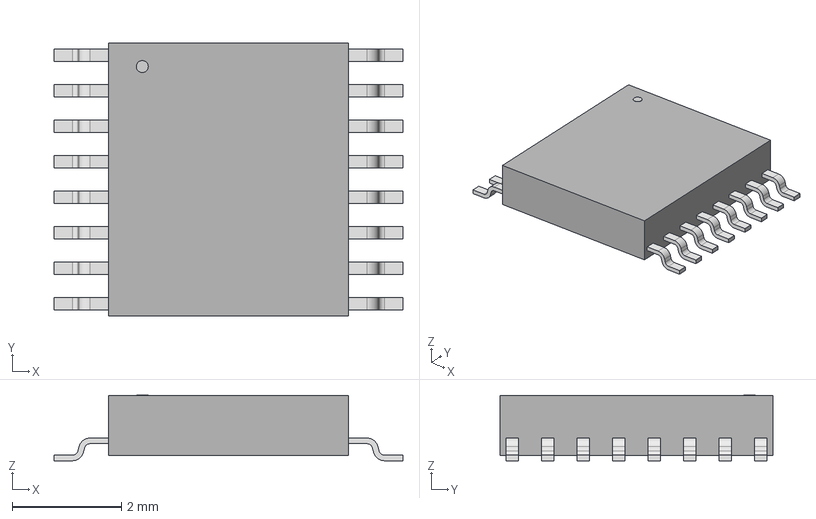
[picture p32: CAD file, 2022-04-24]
pcb/CADmodels/new/P-TSSOP16-0505-0p65-001_TOS.step
6.40 x 5.00 x 1.20 mm

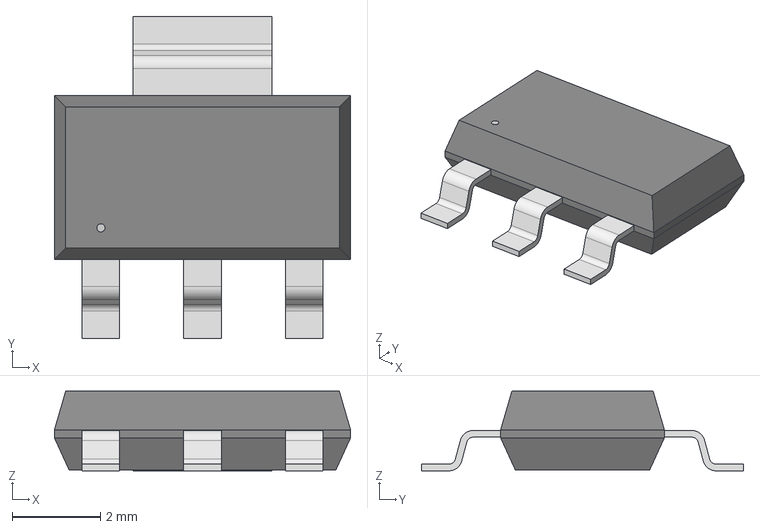
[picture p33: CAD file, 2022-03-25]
pcb/CADmodels/SOT223_STM.step
6.71 x 7.29 x 1.81 mm

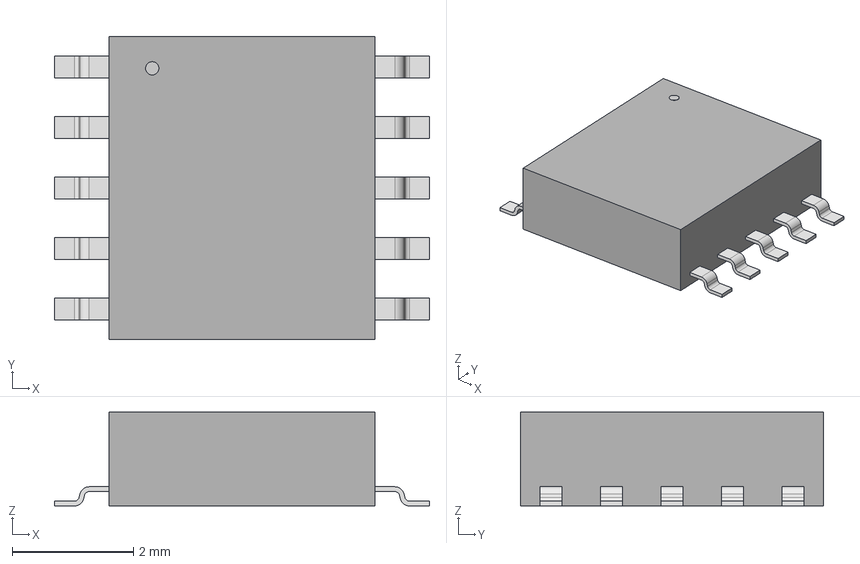
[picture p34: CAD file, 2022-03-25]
pcb/CADmodels/MFP10_4P4X5_ONS.step
6.20 x 5.00 x 1.55 mm

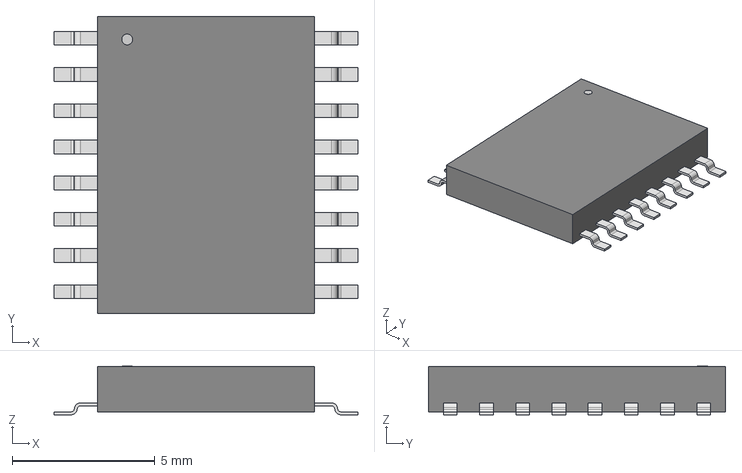
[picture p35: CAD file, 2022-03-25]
pcb/CADmodels/SOT162-1_NXP.step
10.6 x 10.4 x 1.70 mm

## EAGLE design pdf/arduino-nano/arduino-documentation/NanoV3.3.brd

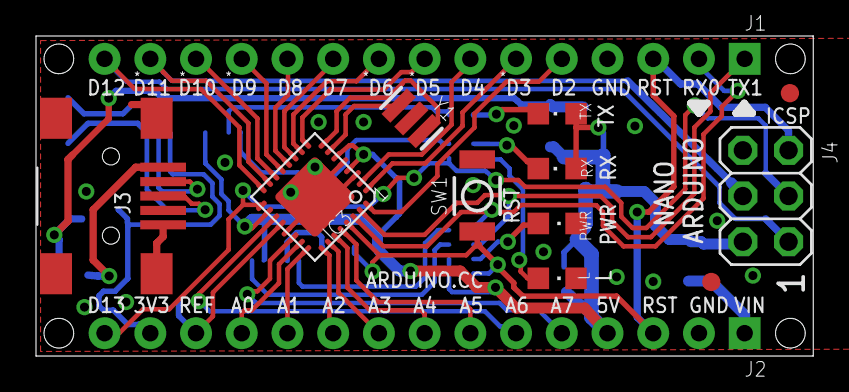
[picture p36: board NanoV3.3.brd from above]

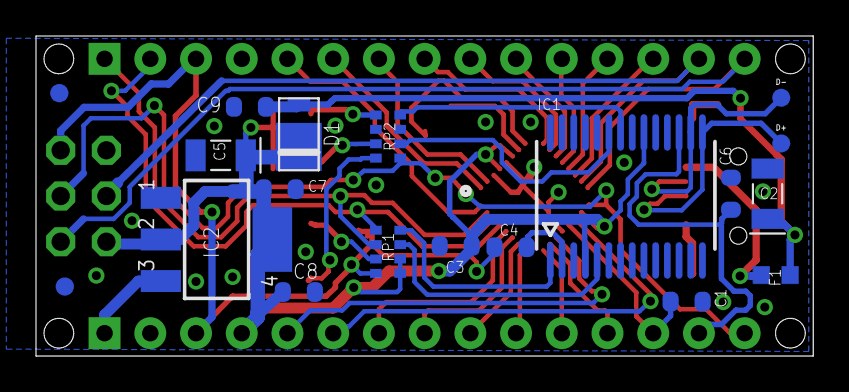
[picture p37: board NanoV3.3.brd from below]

Board: 2 copper layers, 43.2 x 17.8 mm, 33 parts (17 on the bottom side), 43 nets.

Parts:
C1, C4, C6, C9: 100nF; C0603-ROUND
C2, C5: 4,7uF_16V; TAN-A
C3, C7, C8: 1uF; C0603-ROUND
D1: SS1P3L; DO220AAL
D+: DNP; TP-1.00MM
D-: DNP; TP-1.00MM
F1: MFFSMF050; 0603-1608X90N
FRAME1: DNP; FRAME
IC1: FT232RL; SSOP28
IC2: LM1117IMPX-5.0; LINEAR_SOT223
IC3: 328P-MUR; VQFN32
J1, J2: XXXX_STRIPNANO; HEAD15-NOSS
J3: USB-MINI-B_2
J4: 2X03
L: Yellow; CHIPLED_0805
PWR: Green; CHIPLED_0805
RP1, RP2: 1K; CAY16
RX: Red; CHIPLED_0805
SW1: RESET; SMD_157SW
TX: Green; CHIPLED_0805
U$4, U$5, U$53, U$54: DNP; FD-1-1.5
Y1: 16MHz; RESONATOR

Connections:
3V3: C6.2, IC1.17, J2.14
+5V: C3.1, C5.1, C7.1, C8.1, D1.P$1, IC1.4, IC1.20, IC2.2, IC2.4, IC3.4, IC3.6, IC3.18, J2.4, J4.2, RP1.5, RP1.6, RX.A, TX.A
A0: IC3.23, J2.12
A1: IC3.24, J2.11
A2: IC3.25, J2.10
A3: IC3.26, J2.9
A4: IC3.27, J2.8
A5: IC3.28, J2.7
A6: IC3.19, J2.6
A7: IC3.22, J2.5
AREF: C1.1, IC3.20, J2.13
COM: C1.2, C2.2, C3.2, C5.2, C6.1, C7.2, C8.2, C9.2, IC1.7, IC1.18, IC1.21, IC1.25, IC1.26, IC2.1, IC3.3, IC3.5, IC3.21, IC3.33, J1.4, J2.2, J3.1, J3.6, J3.7, J3.8, J3.9, J4.6, L.C, PWR.C, RP2.3, RP2.6, SW1.1, Y1.2
D0/RX: IC3.30, J1.2, RP1.1
D1/TX: IC3.31, J1.1, RP1.2
D2: IC3.32, J1.5
D3: IC3.1, J1.6
D4: IC3.2, J1.7
D5: IC3.9, J1.8
D6: IC3.10, J1.9
D7: IC3.11, J1.10
D8: IC3.12, J1.11
D9: IC3.13, J1.12
D10: IC3.14, J1.13
D11/MOSI: IC3.15, J1.14, J4.4
D12/MISO: IC3.16, J1.15, J4.1
D13/SCK: IC3.17, J2.15, J4.3, RP2.1
unnamed: IC3.8, Y1.3
unnamed: IC3.7, Y1.1
unnamed: PWR.A, RP1.3
unnamed: C4.2, IC1.2
unnamed: D+.X, IC1.15, J3.3
unnamed: D-.X, IC1.16, J3.4
unnamed: L.A, RP2.8
unnamed: IC1.23, RP2.2
unnamed: IC1.22, RP2.4
unnamed: RP2.5, TX.C
unnamed: F1.2, J3.5
unnamed: RP2.7, RX.C
RESET: C4.1, IC3.29, J1.3, J2.3, J4.5, RP1.4, SW1.2
RX: IC1.1, RP1.8
TX: IC1.5, RP1.7
VIN: IC2.3, J2.1
VUSB: C2.1, C9.1, D1.P$2, F1.1

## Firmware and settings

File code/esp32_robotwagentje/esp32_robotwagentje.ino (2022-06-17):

#include <SPI.h>
#include <Wire.h>
#include <Adafruit_GFX.h>
#include <Adafruit_SSD1306.h>
#include <LiquidCrystal_I2C.h> // https://github.com/johnrickman/LiquidCrystal_I2C (install as zip)
#include <WiFi.h>              // Standard ESP32 Library
#include <PubSubClient.h>      // https://github.com/knolleary/pubsubclient (intall with library Manager)

// OLED code from Adafruit example for Monochrome OLEDs based on SSD1306 drivers
// Wifi and MQTT code from Maarten Luyts and from IoT Experiments

// VARIABLES -----------------------------------------------------------------------------------------------------
// WIFI Credentials
// Connect to Hotspot on mobile phone
const char* WIFI_SSID = ""; // Fill wifi SSID between quotes
const char* WIFI_PASS = ""; // Fill wifi pass between quotes
const char* NAAM = "robotwagentje";  // constant to make it easier to set the name for MQTT


//MQTT Information
const char* MQTT_SERVER = "";
const char* TOPIC_MODUS = "robotwagentje/modus";
const char* TOPIC_CMD = "robotwagentje/cmd";


// WIFI and MQTT class instances
WiFiClient espClient;
PubSubClient client(espClient);

// Buffer to store MQTT messages
char msg[4]; //we only need an array of 3 chars because the payload should be between 0-255,
char topic[4]; //but just in case, we take an extra char for an end sign like \0

const uint16_t PWM_FREQUENCY = 500;
const byte PWM_RESOLUTION = 8;
const byte PWM_MAX_DC = 255;


// Motor PWM Pin declarations
const byte PWM_CHANNEL_COUNT = 4;
const byte MOTOR_COUNT = 2;
byte MOTOR_PINS[PWM_CHANNEL_COUNT] = {18, 5, 2, 15}; //we use pin 2 and 5 as direction pin and pin 18 and 15 as speed pin
byte MOTOR_CHANNELS[PWM_CHANNEL_COUNT] = {0, 1, 2, 3};


// LED PWM Pin declarations - DO NOT CHANGE
const int LED_CHANNEL_COUNT = 4;
const int LED_COUNT = 4;

int LED_PINS[LED_COUNT] = {13, 12, 14, 27};
int LED_CHANNELS[LED_CHANNEL_COUNT] = {4, 5, 6, 7};
int LED_STATE[] = {0, 0, 0, 0};


// Linetracker
const byte LINETRACKER_LENGTH = 8;
byte linetracker[LINETRACKER_LENGTH] = {0, 0, 0, 0, 0, 0, 0, 0};
int LINETRACKER_ADDRESS = 8;
int LINETRACKER_REQUEST_SIZE = 1;
byte linetrackerInput = B11111111;         // 1 geeft niks gedetecteerd of uit, dan doen we niks, dus dit is ook de default waarde.

// Distance sensors / afstandssensoren
int DISTANCE_ADDRESS = 16;
int DISTANCE_REQUEST_SIZE = 2;
int distance = 0;
const int MIN_DISTANCE = 10; //cm 


// I2C OLED Display
#define SCREEN_WIDTH 128 // OLED display width, in pixels
#define SCREEN_HEIGHT 32 // OLED display height, in pixels

// Declaration for an SSD1306 display connected to I2C (SDA, SCL pins)
// The pins for I2C are defined by the Wire-library. 
#define OLED_RESET     -1 // Reset pin # (or -1 if sharing Arduino reset pin)
#define SCREEN_ADDRESS 0x3C ///< See datasheet for Address; 0x3D for 128x64, 0x3C for 128x32
Adafruit_SSD1306 display(SCREEN_WIDTH, SCREEN_HEIGHT, &Wire, OLED_RESET);

#define NUMFLAKES     10 // Number of snowflakes in the animation example

#define LOGO_HEIGHT   16
#define LOGO_WIDTH    16
static const unsigned char PROGMEM logo_bmp[] =
{ 0b00000000, 0b11000000,
  0b00000001, 0b11000000,
  0b00000001, 0b11000000,
  0b00000011, 0b11100000,
  0b11110011, 0b11100000,
  0b11111110, 0b11111000,
  0b01111110, 0b11111111,
  0b00110011, 0b10011111,
  0b00011111, 0b11111100,
  0b00001101, 0b01110000,
  0b00011011, 0b10100000,
  0b00111111, 0b11100000,
  0b00111111, 0b11110000,
  0b01111100, 0b11110000,
  0b01110000, 0b01110000,
  0b00000000, 0b00110000 };


//  Enums: Modi, commands and motor direction
enum MODI {                
    MANUAL,
    AUTO,
    PATTERN,
    MENU
};

enum COMMANDS {
    FORWARD,                
    RIGHT,
    LEFT,
    STOP,
};

enum MOTOR_DIRECTION {
    MOTOR_BACKWARDS = -1,
    MOTOR_STOP = 0,
    MOTOR_FORWARD = 1
};

byte modus = MENU;
byte previousModus = 0;
byte command = STOP;
byte previousCommand = 0;

byte drivingSpeed = 128;
const byte TURN_DELAY = 200; //ms

bool lineDeviationLeft = false;
bool lineDeviationRight = false;
bool lineLost = false;

// FUNCTIONS ------------------------------------------------------------------------------------------------------
// Function to setup wifi - DO NOT CHANGE
void setup_wifi() {
    delay(10);
    // We start by connecting to a WiFi network
    Serial.println();
    Serial.print("Connecting to ");
    Serial.println(WIFI_SSID);
  
    WiFi.begin(WIFI_SSID, WIFI_PASS);
    //Display that we still are trying to connect
    while (WiFi.status() != WL_CONNECTED) {
      delay(500);
      Serial.print(".");
    }
    // Normaly the wifi will connect very fast. If it hangs reset the controller with EN button
    // This needs to be done after the controller is programmed
  
    // Print connection information
    Serial.println("");
    Serial.println("WiFi connected");
    Serial.println("IP address: ");
    Serial.println(WiFi.localIP());
}

// Function to (re)connect to the MQTT server - DO NOT CHANGE
void reconnect() {
  // Loop until we're reconnected
  while (!client.connected()) {
    Serial.print("Attempting MQTT connection...");
    // Attempt to connect
    if (client.connect(NAAM)) {//we replaced the literal by a string, so it is easier to configure
      Serial.println("connected");
      // Subscribe
      client.subscribe(TOPIC_MODUS);
      client.publish(TOPIC_MODUS, "connected topic modus");
      client.subscribe(TOPIC_CMD);
      client.publish(TOPIC_CMD, "connected topic command");
    } else {
      Serial.print("failed, rc=");
      Serial.print(client.state());
      Serial.println(" try again in 5 seconds");
      // Wait 5 seconds before retrying
      delay(5000);
    }
  }
}

//This function is called when MQTT receives a message
void callback(char* topic, byte* message, unsigned int length) {
  memset(topic, '\0', sizeof(topic));   // clear the execisting data in the buffer
  memcpy(topic, (char*)topic, length);  // copy the byte array to char array
  Serial.print("topic: ");              // print msg (1/2)
  Serial.println(topic);                // print msg (2/2)
  
  memset(msg, '\0', sizeof(msg));       // clear the execisting data in the buffer
  memcpy(msg, (char*)message, length);  // copy the byte array to char array
  Serial.print("msg: ");                // print msg (1/2)
  Serial.println(msg);                  // print msg (2/2)
}

void oledSetup(){
  // SSD1306_SWITCHCAPVCC = generate display voltage from 3.3V internally
  if(!display.begin(SSD1306_SWITCHCAPVCC, SCREEN_ADDRESS)) {
    Serial.println(F("SSD1306 allocation failed"));
    for(;;); // Don't proceed, loop forever
  }

  // Show initial display buffer contents on the screen --
  // the library initializes this with an Adafruit splash screen.
  display.display();
  delay(2000); // Pause for 2 seconds

  // Clear the buffer
  display.clearDisplay();

  // Draw a single pixel in white
  display.drawPixel(10, 10, SSD1306_WHITE);

  // Show the display buffer on the screen. You MUST call display() after
  // drawing commands to make them visible on screen!
  display.display();
  delay(2000);
  // display.display() is NOT necessary after every single drawing command,
  // unless that's what you want...rather, you can batch up a bunch of
  // drawing operations and then update the screen all at once by calling
  // display.display(). These examples demonstrate both approaches...
}

void oledScrollText(String text){
  display.clearDisplay();

  display.setTextSize(2); // Draw 2X-scale text
  display.setTextColor(SSD1306_WHITE);
  display.setCursor(10, 0);
  //display.println(F("scroll"));
  display.println(text);
  display.display();      // Show initial text
  delay(100);

  // Scroll in various directions, pausing in-between:
  display.startscrollright(0x00, 0x0F);
  delay(2000);
  display.stopscroll();
  delay(1000);
  display.startscrollleft(0x00, 0x0F);
  delay(2000);
  display.stopscroll();
  delay(1000);
  display.startscrolldiagright(0x00, 0x07);
  delay(2000);
  display.startscrolldiagleft(0x00, 0x07);
  delay(2000);
  display.stopscroll();
  delay(1000);
}

void i2cMasterRead(int slave_address, int dataLength, int *input){
  Wire.requestFrom(slave_address, 1);    

  while(Wire.available()) { 
    *input = Wire.read();
    Serial.print("input="); Serial.println(*input, BIN);
  }
  delay(200);
}

void readLinetrackerI2C(){
  Wire.requestFrom(LINETRACKER_ADDRESS, LINETRACKER_REQUEST_SIZE);    

  while(Wire.available()) { 
    linetrackerInput = Wire.read();
    Serial.print("linetracker data="); Serial.println(linetrackerInput, BIN);
  }
  delay(200);
}

void readDistanceI2C(){
  Wire.requestFrom(DISTANCE_ADDRESS, DISTANCE_REQUEST_SIZE);    

  while(Wire.available()) { 
    byte l = Wire.read();
    byte h = Wire.read();
    distance = l + (h << 8);
    Serial.print("distance data="); Serial.println(distance);
  }
  delay(200);
}

void checkLinetrackerDeviations(){
  //lineDeviationLeft
  //lineDeviationRight
  //lineLost
}


// STATE MACHINES -------------------------------------------------------------------------------------------------
//void driveMotors(int leftMotorDirection, int leftMotorSpeed, int rightMotorDirection, int rightMotorSpeed) {
//  ledcWrite(3, rightMotorSpeed);//set the speed to the speedpin
//  ledcWrite(0, leftMotorSpeed);
//  switch (leftMotorDirection) {
//    case 0:
//      ledcWrite(1, 0); //put both pins of the left motor off so the motor doesn't turn
//      ledcWrite(0, 0);
//      break;
//    case -1:
//      ledcWrite(1, 255); //if the motor doesn't turn correctly, replace 0 by 255 or vice versa
//      break;
//    case 1:
//      ledcWrite(1, 0); //if the motor doesn't turn correctly, replace 0 by 255 or vice versa
//      break;
//  }
//  switch (rightMotorDirection) {
//    case 0:
//      ledcWrite(2, 0); //put both pins of the right motor off so the motor doesn't turn
//      ledcWrite(3, 0);
//      break;
//    case -1:
//      ledcWrite(2, 0); //if the motor doesn't turn correctly, replace 0 by 255 or vice versa
//      break;
//    case 1:
//      ledcWrite(2, 255); //if the motor doesn't turn correctly, replace 0 by 255 or vice versa
//      break;
//  }
//}

void modusMenu(){
  if(modus != previousModus){
    Serial.println("Modus change!");

    switch(modus){
      case MANUAL:
        oledScrollText("manual modus");
        modusManual();
        break;
      case AUTO:
        oledScrollText("auto modus");
        modusAuto();
        break;
      case PATTERN:
        oledScrollText("pattern modus");
        modusPattern();
        break;
      default:
        oledScrollText("modus menu: select a modus");
        break;
    }
  }
  previousModus = modus;
}

void modusManual(){
  if (command != previousCommand) {
    Serial.print("Command: "); Serial.println(command);
    
    switch (command) {
      case FORWARD: // Drive forward
        //driveMotors(MOTOR_FORWARD, drivingSpeed, MOTOR_FORWARD, drivingSpeed);
        oledScrollText("forward");
        break;
      case RIGHT: // Turn right around center point chassis
        //driveMotors(MOTOR_BACKWARDS, drivingSpeed, MOTOR_FORWARD, drivingSpeed);
        oledScrollText("right");
        break;
      case LEFT: // Turn left around center point chassis
        //driveMotors(MOTOR_FORWARD, drivingSpeed, MOTOR_BACKWARDS, drivingSpeed);
        oledScrollText("left");
        break;
      default: // Stop driving
        //driveMotors(MOTOR_STOP, 0, MOTOR_STOP, 0);
        oledScrollText("stop");
        break;
    }
    previousCommand = command; //Another question on the assignment, why is this statement necessary
    //-> we will store the last command received from mqtt into an integer, so we can determine in the next run of the loop if we
    //received new data and if so, we will see which command it is and execute the needed code for that command
  }
}

void modusAuto(){
  readDistanceI2C();

  if(distance < MIN_DISTANCE){
    if(random(0,1)){
      //driveMotors(MOTOR_FORWARD, drivingSpeed, MOTOR_BACKWARDS, drivingSpeed);
      oledScrollText("left");
      delay(TURN_DELAY);
    }
    else{
      //driveMotors(MOTOR_BACKWARDS, drivingSpeed, MOTOR_FORWARD, drivingSpeed);
      oledScrollText("right");
      delay(TURN_DELAY);
    }
  }
  else{
    //driveMotors(MOTOR_FORWARD, drivingSpeed, MOTOR_FORWARD, drivingSpeed);
    oledScrollText("forward");
  }
}

void modusPattern(){
  readLinetrackerI2C();
  checkLinetrackerDeviations();

  if(lineDeviationLeft){
    //driveMotors(MOTOR_FORWARD, drivingSpeed, MOTOR_BACKWARDS, drivingSpeed);
    oledScrollText("left");
    delay(TURN_DELAY);
  }
  else if(lineDeviationRight){
    //driveMotors(MOTOR_BACKWARDS, drivingSpeed, MOTOR_FORWARD, drivingSpeed);
    oledScrollText("right");
    delay(TURN_DELAY);
  }
  else if(lineLost){
    //driveMotors(MOTOR_STOP, 0, MOTOR_STOP, 0);
    oledScrollText("Line lost. Stopping and exiting modus.");
    modus = MENU;
  }
  else{
    //driveMotors(MOTOR_FORWARD, drivingSpeed, MOTOR_FORWARD, drivingSpeed);
    oledScrollText("forward");
  }
}


// SETUP ----------------------------------------------------------------------------------------------------------
void setup() {
  Wire.begin();

  Serial.begin(9600);

//    // init of the PWM Pins
//    for (int i = 0; i < PWM_CHANNEL_COUNT; i++) {
//      ledcSetup(MOTOR_CHANNELS[i], PWM_FREQUENCY, PWM_RESOLUTION);
//      ledcAttachPin(MOTOR_PINS[i], MOTOR_CHANNELS[i]);
//    }
//    driveMotors(MOTOR_STOP, 0, MOTOR_STOP, 0); //put every motor off since when the ESP starts up, the motors start spinning
//    //init of the LED Pins
//    for (int i = 0; i < LED_COUNT; i++) {
//      ledcSetup(LED_CHANNELS[i], PWM_FREQUENCY, PWM_RESOLUTION);
//      ledcAttachPin(LED_PINS[i], LED_CHANNELS[i]);
//    }
  
  oledSetup();

  setup_wifi();

  client.setServer(MQTT_SERVER, 1883);
  client.setCallback(callback);
}


// INFINTE LOOP ----------------------------------------------------------------------------------------------------
void loop() {
  readLinetrackerI2C();

 // every loop checks if there is a connection with the MQTT server if not reconnect
  if (!client.connected()) reconnect();

  // every loop we will run the MQTT loop and trigger the callback function if neccesary
  client.loop();

  //convert the msg Array TO Integer
  //since we need an integer to compare to, we need to change the variable type, that's where atio comes into play
  if(topic == "modus") modus = atoi(msg);
  if(topic == "cmd") command = atoi(msg);

  modusMenu();
}

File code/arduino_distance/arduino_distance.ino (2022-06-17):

#include <Wire.h>

// Arduino I2C Slave
#define SLAVE_ADDRESS 16
#define PAYLOAD_SIZE 2
// A5 / PC5 = SCL     // A4 / PC4 = SDA

//const int ECHO_PIN = PB0;
//const int TRIG_PIN = PD7;
const int ECHO_PIN = A0;
const int TRIG_PIN = A1;
const byte ADDRESS = 8;
volatile bool isRequest = false;
bool isDistanceCalculated = false;
long duration = 0;
int distance = 0;

void requestEvent(){
  isRequest = true;
}

// Function from https://create.arduino.cc/projecthub/abdularbi17/ultrasonic-sensor-hc-sr04-with-arduino-tutorial-327ff6
void calculateDistance(){
  isDistanceCalculated = false;
  digitalWrite(TRIG_PIN, LOW); // Clears the TRIG_PIN condition
  delayMicroseconds(2);
  digitalWrite(TRIG_PIN, HIGH); // Sets the TRIG_PIN HIGH (ACTIVE) for 10 microseconds
  delayMicroseconds(10);
  digitalWrite(TRIG_PIN, LOW);
  
  duration = pulseIn(ECHO_PIN, HIGH); // Reads the ECHO_PIN, returns the sound wave travel time in microseconds
  distance = duration * 0.034 / 2; // Speed of sound wave divided by 2 (go and back)
  
  Serial.print("Distance: "); // Displays the distance on the Serial Monitor
  Serial.print(distance);
  Serial.println(" cm");
  isDistanceCalculated = true;
}

void setup() {
  //pinModeAllToInput();    // Pin reset

  pinMode(TRIG_PIN, OUTPUT);
  pinMode(ECHO_PIN, INPUT);

  Wire.begin(SLAVE_ADDRESS);
  Wire.onRequest(requestEvent);
  
  Serial.begin(9600);
}

void loop() {
  calculateDistance();
  if(isRequest & isDistanceCalculated){
    Wire.write(distance & 255); 
    Wire.write(distance >> 8); 
    isRequest = false;
  }
}

void pinModeAllToInput(){
  DDRD &= ~(B11111100);
  DDRC &= ~(B01111111);
  DDRB &= ~(B00111111);
}

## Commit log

2022-03-25 Analyse correcties + CAD files
2022-03-25 CAD libraries uitgepakt
    [MFP10_4P4X5_ONS.step, SOT162-1_NXP.step, SOT223_STM.step]
2022-03-25 Schema + PCB
2022-04-16 Arduino Nano replaced with separate components
2022-04-16 USB interface datasheets, schematics, CAD
    [BOM_NanoV3.2_2022-04-16.csv, NanoV3.3.brd, NanoV3.3.sch]
2022-04-17 Button option added
2022-04-17 PCB v2
2022-04-17 Sensorschakeling schema en PCB
2022-04-17 Sensorschakeling schema file
2022-04-18 PCB v2.1
2022-04-18 Sturingsschakeling schema v2.0
    [BOM_NanoV3.2_2022-04-16.csv, NanoV3.3.brd, NanoV3.3.sch]
2022-04-22 ESP32 module analyse update
2022-04-24 Sturingsschakeling v3.1
    [P-TSSOP16-0505-0p65-001_TOS.step]
2022-04-24 Sturingsschakeling PCB v3.1 om in te dienen
2022-05-02 Motor driver IC update v3.1
2022-05-02 Update USB connector en interface v3.1
2022-05-11 Fusion 360 PCB viewer added
2022-05-12 Sensorenschakeling opgesplitst, PCB v1.0 Afstanssensoren en Linetracker
2022-05-12 PCB's in analyse update
2022-05-13 Fabricatie files
    [PnP_Sensorschakeling_Afstandssensoren v9_back.csv, PnP_Sensorschakeling_Afstandssensoren v9_front.csv, PnP_Sensorschakeling_Linetracker v4_back.csv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]
2022-05-19 Update PCB v4.0 voor inhouse fabricatie
2022-05-19 Pictures PCB v4.0
2022-05-19 Sturingsschakeling PCB v4.1
2022-06-16 Updated diagrams
    [PnP_Sensorschakeling_Afstandssensoren v9_back.csv, PnP_Sensorschakeling_Afstandssensoren v9_front.csv, PnP_Sensorschakeling_Linetracker v4_back.csv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]
2022-06-16 PCB prototype foto's
2022-06-16 Update PCB prototype foto's
2022-06-16 PCB prototype foto's upload
2022-06-16 Update PCB foto's

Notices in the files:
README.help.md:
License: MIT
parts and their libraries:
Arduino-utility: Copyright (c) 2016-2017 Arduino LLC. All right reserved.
